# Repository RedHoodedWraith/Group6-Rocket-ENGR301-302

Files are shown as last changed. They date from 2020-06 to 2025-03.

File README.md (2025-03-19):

# Group 6's Rocket Project
## Introduction
This project was developed as part of an in-class group project to design and develop a hobbyist rocket that used on-board programmable electronics to control it and to collect and report on-board telemetry.</br>
It was developed in 2020 by students in Group 6 from the [ENGR301](https://www.wgtn.ac.nz/courses/engr/301/2020) & [ENGR302](https://www.wgtn.ac.nz/courses/engr/302/2020) courses at the Victoria University of Wellington in New Zealand. 

While the students who worked on this project passed the aforementioned courses, at the time of writing, this project is in an unfinished state and there is not functioning rocket.</br>
The courses, ENGR301 & ENGR302, were focused on developing our skills around working on technical projects as part of a development team that uses Agile Development Practices. In the context of the courses above, this project was worked on to put into practice what we had learnt and to demonstrate our skills relating to using Agile.

While this project is incomplete and isn't likely to be worked on, anyone is welcome to use what we have made so far and/or to finish it off.

## Contributors

### Software
* Asami De Almeida
* Ketaki Bagal
* Penny Peneuta

### Hardware
* Jason McCormick
* Sean Osborne-Curtis
* Robert Reid
* Dylan Sukha

### University Staff Involved
* Andre Geldenhuis
* Aaron Chen

## Modules:

### Software Development
* Sun Incinerator Rocket Controller | PID system
* Sensor Test Programs
    * MPLI2C | Barometer + temperature readings.
    * MPU | | Gyro + Acceleartion readings, IMU+Servo Control.

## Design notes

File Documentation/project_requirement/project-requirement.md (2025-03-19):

environmental# ENGR 301: Project Requirements Document

The aim of this document is to specify the requirements of the system your group is to build. The focus of a requirements document is the problem you are attempting to solve:  not a first attempt at a solution to that problem. This document should communicate clearly to the supervisor, client and course coordinator what the system you build is going to do, and what constraints it must meet while doing so.

The document should also demonstrate your understanding of the main analysis principles and quality guidelines, and applicable standards, using tools and notations as necessary to communicate the requirements precisely, unambiguously and clearly in a written technical document. Page specifications below are *limits not targets* and refer to the pages in the PDF generated from the markdown. Because the size of your document is necessarily limited, you should ensure that you focus your efforts on those requirements that are most important to completing a successful system: if sections are at their page limit, indicate how many items would be expected in a complete specification.

The ENGR 301 project proposal and requirements document should be based on the standard ISO/IEC/IEEE 29148:2011(E), primarily sections 8.4 and 9.5, plus section 9.4 for projects involving hardware and ISO 25010 SQuaRE for systemic requirements. While excerpts from the standard have been quoted within the template, to understand what is required it will be necessary to read earlier sections of the standards themselves. A supplementary treatment of requirements gathering in engineering projects may be found in [Requirements in Engineering Projects](https://victoria.rl.talis.com/items/F166DA94-DAD8-FBDB-0785-7A63C9BA3603.html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) (Talis). The requirements document should contain the sections listed below, and conform to the formatting rules listed at the end of this brief.

All team members are expected to contribute equally to the document and list their contributions in section 6 of the document. You should work on your document in your team's GitLab repository. While collective contributions are expected to be the exception rather than the rule, if more than one team member has contributed to a particular commit then all those team member IDs should be included in the first line of the git commit message. `git blame`, `git diff`, file histories, etc. will be tools used to assess individual contributions, so everyone is encouraged to contribute individually, commit early and commit often. Any team wishing to separate individually contributed sections into a single file before collation into the single proposal document for submission is welcome to do so.

---

# ENGR 301 Project *NN* Project Proposal and Requirements Document
#### Author list, a comma-separated list of the names of each member of the team.

## 1. Introduction

### Client

The Client for this project is Andre Geldhuis, and can be contacted by andre.geldenhuis@vuw.ac.nz or through Mattermost.

### 1.1 Purpose

The purpose of this system is to build off an existing rocket system and to improve its avionics and flight control.

### 1.2 Scope

The rocket being made for the client(s) listed above needs to be able to do the following:
*  Thrust itself from ground in order to launch itself into the air
*  Continue to propel itself in a largely vertical direction
*  Self-adjust propellant to its nozzle(s) in order to continue travelling in a controlled upwards direction
*  Travel upwards at a velocity that demonstrates the rocket is being controlled by its on-board control systems

The development of this rocket will happen in 3 core stages. Hardware design stage, software design stage and trial testing.
The Hardware Design Stage will focus on the physical build and design of the rocket, incorporating all the necessary components,
maximising travel efficiency and minimising the physical obstacles. The Software Design Stage will focus on programming the
on-board micro-controller to automatically adjust the rocket's propellants to self-correct the rocket's travel. Trial testing will
involve launching test rockets to observe how it performs in-situ and to return back to either design stages to modify the design to
 its performance. This project's development is limited by a variety of factors, most notably access to the internet and the civil restrictions in place due to the COVID-19 pandemic.
This heavily limits the availability to source parts for the rocket and opportunities to test the physical rocket prototype in-situ.

### 1.3 Product overview
#### 1.3.1 Product perspective

The project, in its entirety, is expected to address and solve the general issue of producing a controlled rocket using open-source software and open-hardware. The intended use for this rocket will primarily be for private operation but carries the potential for extended development and commercial use through being open-source.

The avionics element of the project must imitate the functionalities of a contemporary, off-the-shelf version and provide control features for the rocket as well. In particular, the system is required to manage various components of the rocket that ensure controlled flight such as, sensors, servos motors and transmitters.

In terms of the hardware component, the physical rocket model will be constructed from scratch, adapting the template of a basic hobby rocket that incorporates a gimballing motor for control. Additionally, an avionics board is to be assembled so that data can be remotely collected from the rocket and sensors. The software component will be developed to contribute in designing the control parameters for the avionics board.

The hardware and software components of the avionics package are required to seamlessly communicate with the mission control and simulation segments of the project to ensure a successful launch and flight for the rocket.

The avionics package will communicate with mission control to report its current pre-launch, launch and in-flight status. The simulation software will be used to aid in designing the rocket and determining estimates for the rocket control parameters. In this case, the software model of the control code developed in the avionics package will be required for simulation.

#### 1.3.2 Product functions

One page summary of the main functions of the product (9.5.4), briefly characterising the minimum viable product.

The minimum requirements for this avionics system will consist of the following:
- Record all sensor data which should collect data on a variety of benchmark measurements that include but are not limited to: stability, altitude, deviation, and critical components.
- Achieve an aerodynamically stable and consistent launch
- A demonstration of mission control's ability to adjust flight trajectory post-liftoff by instructing the gimble to turn, performing a kickover.
- After the motor has completed its burn, broadcast telemetry (location) over LoRa modules to a base station on the ground.
- An avionics package that is easy to install and uninstall.
- A hardware "On" and/or "Reset" switch that initialises launch in the event of a software launch failure.
- "Fast" hardware and software setup. Ideally, 10 minutes or less.
- Utilise onboard sensors and tuned error control to prolong vertical traversal. 
- Provide a compatible interface to be used in conjunction with a mission control system.
- Provide a compatible interface utilise simulation data for calibration ahead of time.

Ideally, the finalised package will incorporate the following:
- Support for parachute deployment.
- Provide control for aerodynamically stable launches without a rail.

#### 1.3.3 User characteristics   

The avionics package will be open-source meaning anyone can access it. However, the intended main class of users for this project is the wider model rocketry/high power rocketry community. And so general user characteristics which are expected include:

- An understanding of rocket avionics
- Technical expertise when installing different components of the rocket
- An understanding of those components and how they function within the system
- Technical expertise in telemetry systems
- An understanding of how the software will interact with the hardware
- Experience in operating aircraft applications
- Knowledge in Civil Aviation Authority (CAA) regulations

Due to health and safety concerns users testing the rocket in the field should not have any physical and or mental disabilities that would put them at risk.

#### 1.3.4 Limitations
Within project limitations, the team is faced with several limitations such as;
- Current worldwide affect(COVID-19): COVID-19 has resulted in a nationwide lockdown. This has limited the group options and approach towards the  current project. Certain aspects of the project will be adjusted from the original plan. The use of communication tools like Mattermost and  Zoom  will be crucial to the group.

- Budget: The team has a very limited budget of approximately $333.00 NZD. The budget has designed to be spent on components for the hardware as well as 3D printing for the rocket body.   

- Hardware accessibility: Due to the effect COVID-19 has had on the university, our hardware accessibility is been very limited. The extension of the hardware is improving on the control system of a previous team and on using *Onshape* to improve the design of the body of the rocket. 

- Software: The software aspect of the project is not very limited from the lockdown. The software aspect will consist of improving code from a previous team and ensuring it is functional and efficient.  

- Testing facilities: Due to COVID-19 lockdown, it will be unlikely that a testing facility is available for the group to use. The next step is to do testing via simulation. Working with a simulation team will be required. If circumstances change and access to testing facilities become available then the group will have to discuss the possible option.

- Time: This project runs over two papers ENGR 301 and ENGR 302. This gives the group 30 weeks, however with the first few weeks being introductions realistically the group has about ~27-26 weeks. The lockdown has resulted in a reconstruction of the academic year of Victoria            University of Wellington. This could result in less time.    

- Control & policies: When testing the rocket system we have designed, we need to ensure it is in a controlled environment. We can not breach any laws and restrictions that have been imposed by the government due to COVID-19 and we need follow The NZ Rocketry Association rules and regulations.  

- Team interactions: The main form of communication will be through Zoom and Mattermost due to the level 4 lockdown. Zoom meetings are held every Friday and Monday, and Mattermost chat is constant.

- Personal limitations: All members have personal limitations that should be taken into consideration. This will ensure all members of the group are treated fairly. Other members of the group as well, take other papers. Due dates of important assignments and test will be taken into account, this is design to reduce stress levels of the group.

## 2. References
[1] Civil Aviation Authority of New Zealand, “Civil Aviation Rules, Part 101 Gyrogliders and Parasails, Unmanned Aircraft (including Balloons), Kites, and Rockets Operating Rules” December 31st, 2018 [Online]. 
Available: https://www.aviation.govt.nz/assets/rules/consolidations/Part_101_Consolidation.pdf [Accessed: May 13th, 2020]. 

[2] National Aeronautics and Space Administration, Vectored Thrust, Glenn Research Center, Nancy Hall, 05 May 2015.
https://www.grc.nasa.gov/WWW/K-12/airplane/vecthrst.html

[3] New Zealand Legislation, Radiocommunications Regulations 2001, 10 September 2001. 
http://www.legislation.govt.nz/regulation/public/2001/0240/latest/DLM71513.html. 

[4] The Model Rocket, Model Rocket Engine Sizes and Classifications, Charlie Gasmire, 2020.
https://themodelrocket.com/model-rocket-engine-sizes-and-classifications/

[5] New Zealand Rocketry Association, “Rocket Safety, Model Rocketry Safety Code” [Online]. 
Available: https://www.nzrocketry.org.nz/rocketry/rocket-safety [Accessed: May 13th, 2020]

References to other documents or standards. Follow the IEEE Citation  Reference scheme, available from the [IEEE website](https://www.ieee.org/) (please use the search box). (1 page, longer if required)

## 3. Specific requirements  

This section describes the external interfaces, functions, usability requirements, performance requirements, logical database requirements, design constraints, non-functional system attributes, physical and environment requirements and supporting information.

### 3.1 External interfaces

#### Sensors - Inertial Measurement Unit

The inertial measurement unit (IMU) is an electronic device that measures acceleration, gyroscopic and magnetism data on the avionics package, each in 3 dimensions. This will be used to specifically measure the changes in the linear acceleration, velocity, and orientation of the rocket. The data from this unit will be outputted onto the SD card onboard where the Teensy will also process this information and control the position of the gimbal. This component of the system will require good accuracy plus tolerance as it is vital for the control of the rocket and will need to have a measurable acceleration range suitable for the rocket. The orientation and position of the rocket will be measured on 3 dimensions, in units of metres and degrees respectively. This will be present as part of the onboard avionics package.

#### Data Storage/Transfer - SD Card

An SD card is required to store data that is produced from the IMU, radio antenna, GPS and any other potential sensors. This information is to be processed for control and to be later used for the analysis of the performance of the system. The onboard system will need to be able to write to the SD card at a rate equivalent to the rocket's control loop. This rate will be required to be optimized so that it does not affect processing speed significantly while maintaining maximum control. The SD card must also be large enough to store all the potential data in a test run, with the data being stored in a .txt or .csv file.

#### Communication - Radio Antenna

The radio antenna is required for limited communication of data from the avionics package, using LoRa, to a nearby external computer for monitoring the data and minor adjustments/tuning. The antenna will receive signals from the avionics package and will output transmissions for a receiver antenna. The data sent will be required to be accurate enough to determine the state of the system in real-time and so it can be located easily using the satellite positioning system, GPS, in the case that it is lost. Data transferred during the launch will need to be essential data only as communication should not compromise performance of the control system.  The units of measure for this data will all be SI units and degrees/minutes/seconds for the longitude and latitude. This will play an important role for mission control in the field.

#### Mechanical - Gimbal

The rocket's gimbal will control the angle of the thrust relative to the centre of mass, thus stabilising and controlling the direction of the rocket's propulsion through the launch. This process is known as thrust vectoring. The gimbal will be controlled by the software on the avionics package which will adjust servos, altering the pitch and yaw. This will require a closed-loop control such as a Proportional-Integral-Derivative system, input from the IMU and outputting to the Gimbal.

#### Control Hardware - Servos

Two servo motors will be required to control the gimbal, that is controlled by an electric signal which determines the movement/angle of the shaft. This will be controlled from the avionics package and will alter the orientation of the gimbal. The servo's shaft rotation will be measured in degrees. The two motors will work individually, one to control the pitch and the other yaw. The timing response of this part is required to be minimised so that the rockets projection control can be as close to instantaneous as possible.

#### Ejection Ignition

The rocket will require a system to fire small igniters, which serve as ejection charges for the parachute. These are to be set off at a predetermined height for the descent of the rocket. This will receive its signal from the avionics package, which determines the height using the onboard barometer sensor. Some precaution is also required for the development of this component, as it will need to be ensured that it won't fire while the rocket is being handled.

#### Motor

The motor is a single-use component to produce the thrust for the rocket during the launch, by burning through a propellant which is released through a nozzle to produce powered flight. The ignition is required to be controlled by an electric igniter externally from the rocket for safety. This motor is to be connected to the gimbal, which will control the rocket. Motors vary in size depending on their total impulse, measured in Newton Seconds. This rocket will be required to use motors in the range of classes from C to G, ranging from 5-160 Ns. These motors likely to have a diameter of 24mm, and some of the smaller ones being 18mm.

### 3.2 Functions

> List up to fifty use cases (in order of priority for development),

#### Stakeholder Requirements:
- Avionics package must entirely fit inside the rocket's shell.
- Avionics package must interface with the gimbal.
- Avionics package must guide rocket on course.
- Avionics package must stabilise the rocket so it stands in an upright position while preparing for launch.
- Avionics package logical database will be comprehensible in the form of a text file.
- Avionics package should be comprised of fixated and durable components.
- Avionics package in the rocket must interface intuitively with the base station.
- Avionics package must ensure onboard power management can cope with each stage of the rocket's execution.

#### Use Cases:
Upon delivery to the primary client (Andre), the extended branch of stakeholders will include open-source hobbyists.
The purpose of this avionics package is to provide control and guidance for the rocket.
To do so, it needs to be installed, configured and calibrated prior to launch.
The user(s) should be able to expect recorded data from the flight.
The typical usage of the avionics package would look like:
Installation, calibration, launch, and post-flight analysis.

##### Installation
For ease of installation and reinstallation, the avionics package will uphold the following:
- Minimal physical footprint to mitigate spatial occupation and excess weight.
- Ensure as many components are fixated on a single unit rather than having components loose and untethered.
- Trouble-free pairing with the base station.

##### Configuration and Calibration
- The avionics package should be easy to configure for all intended stakeholders.
- The finished package should not require re-engineering to interface with control software during launch setup.
- Calibration data from simulations should be preloaded and initialised onto the avionics package prior to launch. Calibration is crucial as the standalone error control is likely not adequately fast enough to ensure stable control of the rocket.
- The calibration data will be stored on the SD card onboard the avionics package.
##### Launch
Once the rocket is launched into powered flight, the rocket will be remotely controlled via the gimbal to sustain vertical trajectory.
Vital flight data will be communicated with the base station in real time.
At the stage of burnout, the avionics package will be automated to deploy the parachute as a step to mitigate risk during the process of landing.
##### Analysis
The avionics package should broadcast vital data via its wireless antenna to the base station during flight. <br></br>
When the active flight is over, all logged data (measurements, instructions and gimbal positions) should be stored to the SD card, as a text file in a human-readable format.
If the avionics package is still in range of the wireless signal, it will attempt to broadcast the data to mission control. All data broadcasted to mission control must comply with the standards (units, parsing methods, encryption etc) of the mission control software.

### 3.3 Usability Requirements

The avionics package is usable if it is efficient and can successfully be operated and applied by no less than a rocket hobbyist. Therefore, the goal is to create an open-source avionics package that is accessible to the wider avionics community and applicable in all types of rocket-related use. The rocket should also be able to perform and endure through various external factors such as wind. This means that it is important to build a versatile avionics package that can withstand the external factors and mitigate the risks that follow.

In context, the avionics package will be used as a major component of a controlled rocket launch system. The effectiveness of the avionics package is measurable by its performance, which is contingent upon the success rate of a favourable launch and flight.

This is achieved by performing frequent in-flight correction of the gimbal position to ensure high efficiency and furthermore high performance. The software model of the avionics package will need to be designed in a way where it can easily be applied by the simulation segment of the larger system. As a result, this will contribute to improving the performance of the rocket gimbal.

Additionally, the software model should ideally be written using a common programming language used in avionics such as C to further improve its usability in the future. This will ensure that the software can be understood and applied by the regular avionics user.

In terms of the hardware component, it is essential that the avionics package is constructed in a way that is adaptable to changes that can occur at any point in time. The manual controls on the rocket should also be easily accessible to the user even after construction is completed.

**Uses**

Launch:

The rocket must be ready for launch within a set period of time following system activation.

In-flight:
- Diagnostics: The data from the rocket and sensors are remotely collected. This will diagnose any in-flight issues with the rocket.
- Recovery Mode: Once the motor burns out, recovery mode is enabled and the parachute is ejected.  

### 3.4 Performance requirements

This section defines the expectations of the rocket's functions and qualities, what the product should demonstrate to the user on a quantitative and qualitative level. The rocket will be constructed of many different functioning components, establishing a range of software and hardware performance requirements along with the rocket's general performance itself.

A key requirement of the rocket's performance is that it has a strong structural integrity, so that it is able to withstand stress, acceleration, velocity, vibration and heat that will be present during launch. This will ensure functionality and longevity of the rocket. It is required that the system can be tested at least 10 times, with any deficient parts after that to be easily replaced. The environment has a strong impact on the performance of the rocket, the most critical factor being the wind. Ideally the rocket will launch when there is minimal wind however this can be expected to increase with altitude. The system will be required to control the rocket in wind speeds up to 15 m/s. The general performance of the system is required to have a vertical-to-horizontal distance travelled ratio exceeding 90% at the completion of climbing flight.

The performance of the software will have a strong influence on the rocket's control so the system will require minimum delay between sensors and actuators. This delay will be determined by the maximum operating speeds of the components, such as the servos and the IMU. Another key aspect of the software performance is the communication of data through out each stage of the launch. It is essential that information to mission control is continuous. It is important to note that however this load will vary depending on the stage. The required data is the state of the rocket, the location and potentially some kinetic data. An additional software requirement is for a fast data rate on to the SD card, which will need to be taking readings from the sensors at least every 50ms more good analysis of the flight.

The core part of the systems performance is dependent on a power supply which makes the batteries performance vital. It is required that the system does not deplete more than 50% of the capacity throughout the launch process, leaving the remaining power for initiation and retrieval. This will be later detailed with more knowledge of the power consumption and specifications. It is also required that the servos are performing at a rotational speed sufficient enough to emulate the control system and also strong enough to manipulate gimbal. The geographical location of the rocket is important for finding it after launch so the GPS is required to perform within an error of 10 metres. To ensure communication during this stage the LoRa radio system will be required to transmit and receive up to 2 kilometres away, so the rocket may be retrieved if it was to travel far during descent. Like the structural integrity of the rocket, the individual components will need be able to with stand the induced environment factors during launch for longevity, this will require strong connections and a good quality of wiring. A vital part of the systems performance is that it is required to eject a parachute at the top of ascent, this needs to be certain so tests will be required to be implemented.

### 3.5 Logical database requirements

In order to analyse the system that will be implemented, the use of a domain model for the purpose of demonstrating the logical database requirements would be useful. For the purposes of this design, elements that will be implemented include the use of inertial motion unit (IMU) that are the sensors that collect the data that will be provided for the use of the overall system, including the controller. Additionally, this data will be fed into a microcontroller. Additional data that will be fed into the microcontroller is the GPS data. However, this data will not be used for the actual control of the system. Furthermore, data from the microcontroller will be sent to the SD Card Data Writer for the purpose of locally saving the flight data. And finally, there will be a radio module that will be used to broadcast the data to mission control remotely.

@startuml

title Relationships - Class Diagram

class IMU {
  +Gyrometer
  +Acceleromter
  +Magnetometer
}

class Microcontroller
class RadioModule
class GPSModule
class SDCardWriter

IMU --> Microcontroller
GPSModule --> Microcontroller
Microcontroller --> SDCardWriter
Microcontroller --> RadioModule

@enduml

**Gyroscope**

A gyroscope will collect data with reference to the potential rotation of the rocket with reference to the ground. This will be a key data point for the determination by the microcontroller on if or when any changes need to be made with respect to the gimble. Rotational energy that deviates outside of an expected range could lead to the rocket flying fully off course or even catastrophic failure.

**Accelerometer**

This device will measure the change in velocity and acceleration with reference to the acceleration of gravity. This data can be used to determine altitude which will be  a key point for the determination of apogee and the initialisation of any recovery hardware.

**Magnetometer**

A magnetometer in this device can be used for the purpose of designing a form of a digital compass that can determine which side of the rocket is facing a given cardinal direction with respect to the magnetic north pole. This data would be useful for the purpose of the microcontroller to determine if any gimbal adjustments need to be made if there is an imbalance in the rocket. Or, in other words, the mass of the rocket is not centred around a centre point of a cylindrical shape.

**GPS Module**

The device will be used to collect positional data at the cessation of the rocket launch to determine where the rocket's landing area is. This is particularly useful if there is an extreme deviation of the rocket landing area from the rocket launch area.

**Microcontroller**

The microcontroller will handle the general integration of all the IMU componenets. This collective data will be interpreted by the microcontroller to determine if any positional changes to the control gimble will need to be made. Accurate and calibrated data collection is essential for any practical use of the microcontroller for this system.

**SD Card Writer**

The SD card writer will be the component that keeps the log of all the data collected during the flight from the IMUs. Furthermore, it will log any changes made to gimble positions. Furthermore, these can be timestamped to correspond with specific values from the IMUs including any data that is calculated by the microcontroller for the purpose of determining flight changes. These could include altitude, reduction in acceleration, positional data, etc. 

**Radio Module**
The radio module will retain the purpose of being able to send radio data (including that which would be written to the SD card) to mission control. The collection of this data during flight would allow for mission control to determine if any manual changes need to be made that override the microcontroller. As such, this radio module would also need to be able to receive signals from mission control. 

You should use right tools, preferably PlantUML, to draw your URL diagrams which can be easily embedded into a Markdown file (PlantUML is also supported by GitLab and Foswiki).

### 3.6 Design constraints

**Software - Open Source**

For the final avionics package to qualify as open-source, only open-source resources may be used throughout its development. The open-source resources used must be well documented and credited, where needed, in the package release. Softwares, which are not open-source, may only be used if absolutely necessary and has been consented by the client. Once finished all source code for the package must be released in accordance with the open source definition.

**Software - API**

For consistency and compatibility across the three different sections, system engineering, mission control and rocket simulations, the same API should be used. Using the same API also ensures that the final avionics package will work as a whole.

**Hardware - Radio Antenna and the Satellite Navigation System Unit**

The radio antenna must follow the New Zealand Legislation, Regulation 9 of the Radiocommunications Regulations 2001 and only use the legally available frequencies with the rockets and solely for their intended purpose [3].

Similarly, the satellite navigation system unit used must also follow the New Zealand Legislation, Regulation 9 of the Radiocommunications Regulations 2001 and only use the legally available satellite navigation frequencies for New Zealand [3].

To avoid interference with nearby devices the radio antenna must use frequencies with the least use. Interference with other devices may result in corrupted data, which in turn could affect the satellite navigation system location of the rocket.

**Hardware - Physical Construction**

In accordance with the New Zealand Civil Aviation Authority and the New Zealand Rocketry Association, the rocket at its maximum size must satisfy the following criteria [1][5]:

- The rocket cannot use more than 125g of propellant
- The rocket cannot produce more than 320 Newton seconds of total impulse
- The rocket must use a slow-burning propellant
- The rocket is made from lightweight materials such as paper, wood, rubber and or plastic
- The rocket must not have the nose cone, fins or body fabricated from metal
- The rocket must not exceed a gross mass (i.e. including the propellant) of 1.5kg
- The rocket must not use an aerial firework as an ingredient to form its own jet
- The rocket must only use certified commercially-made model rocket motors
- The rocket motors must only be used in line with the manufacturer's recommendations (i.e. no tampering)
- The rocket must be launched with an electrical launch system and electrical motor igniters

The physical construction of the rocket will also be limited to our budget, what we have access to in the labs and (due to Covid-19) when. Similarly delays in shipments because of the virus will also limit us in what parts we can order online.

### 3.7 Nonfunctional system attributes

Present the systemic (aka nonfunctional) requirements of the product (see ISO/IEC 25010).
List up to twenty systemic requirements / attributes.
Write a short natural language description of the top nonfunctional requirements (approx. five pages).

1. Safety
   - The rocket's operations must not cause nor contribute to harm or death to people or animals, including but not limited to its operators, nearby bystanders, pets and the local biodiversity.
   - The rocket's operations must not cause damage to property nor the local environment external to its operational scope. Example: Burnt Fuel Residue to the launchpad is accepted as it is expected as part of its operation. Cracking the windscreen of a nearby vehicle is not acceptable.
   - Operators must be able to know sufficient real time information with regards to the condition, location and effects of the rocket during its operation.

1. Flight
   - The rocket needs to be able to thrust itself from the launchpad.
   - The rocket needs to be able to continue to propel itself upward when it is expected to do so.
   - The force exerted by the propellant needs to exceed the opposing forces, such as the force of gravity onto the rocket's mass and air resistance.

1. Robustness
   - The essential systems contributing to the rocket's flight must remain sufficiently intact during the rocket's operation.
   - Obstacles must not compromise the rocket's essential system processes that allows it to function.
   - The essential systems that contribute to the rocket's flight must be able to continue functioning when performing its task.
   - Essential system operations must not compromise each other system's functionality during their operations.

1. Control
   - The rocket's operation (during flight) must be sufficiently controlled by its operators.
   - Any unintended effects from the rocket's operation must be able to brought back into the control of the operators.
   - The rocket must be able to be controllable in order to increase Safety.
   - The rocket must be able to be brought back to a stationary or non-functioning state when expect it is expected to.
   - The rocket must be able to travel along the intended flight path of the operators' choosing.

1. Trackability
   - At minimum, sufficient data of the rocket's operation must be available to rocket's operators during its operation. This means data expected to be delivered in real time during the rocket's operation must be delivered in real time.
   - The rocket's location must be able to be monitored and known at all times during its operation, as per the requirement of Saftey and the Client's requirement.
   - Essential data that is not expected to be collected in real-time, must be able to be retrieved after the rocket's operation has ended.

1. Legal
   - This project must be performed legally and with the permission of the applicable property owner(s).
   - What we make and test must adhere to the rules and regulations of the relevant local authorities

### 3.8 Physical and Environmental Requirements
The system Hardware components:
- microcontroller(Teensy 3.6)
- gyroscope/accelerometer sensor
- sensor module(IMU)
- wireless antenna
- rocket motors
- servos
- gimble
- parachute + ejection charge
- rocket body
- launch pad (this includes, barometer, gps and the base station)

The hardware components must be able to still function within the environment that the rocket will be tested in, this means that the rocket will need to function under certain enviromental condition(s) that are present in the testing environment. The current testing environment is a wide-open park located in Upper Hutt, Wellington. A certain environmental condition is the wind. Wind levels are never constant and can vary extremely (especially in our testing environment of Upper Hutt Wellington). This means hardware of the rocket must be functioning under considerable wind levels. 

The largest effect wind has on the rocket is displacement. The wind is able to tilt (or even move) the rocket off its current trajectory. This means that hardware of the rocket must be to account for this issue. Combination of the electronic components (microcontroller, gyroscope and sensor module) and the gimble are involved in accounting for the displacement. Using the sensor(s) to detect the displacement, then micro-controller communicates to the gimble to make an adjustment for the displacement.

The rocket body design is also important to account for wind. A more aerodynamic design will mean that the wind drag will have less of the effect of the rocket. Meaning a more aerodynamic design will result in a smaller displacement.

Wind will also greatly affect the rocket while the rocket is coming down. The rocket slowly descend due to the parachute being deployed. However, with the parachute deployed the rocket is very susceptible to wind drag. Which means that the rocket might be displaced a large distance from the launch site. A GPS connected to the micro-controller will allow us to track where the rocket lands. Also, modelling of the rockets launch will be done to estimate where the rocket could land.

Another environmental condition that will need to be taken into account is radio frequency (RF) noise. To communicate to the rocket microcontroller we use a signal in the microwave frequency. So before we can launch the rocket, we will need to check the level of RF noise. If the level of RF noise is too high the launch of the rocket will be postpone, there is no solution where we launch the rocket in high RF noise. If the rocket is launch in during high RF noise we could lose communication with the rocket.

Certain envionmental conditions like rain, high cloud coverage and extreme temperatures will mean that the rocket launch won’t be able to happen. However, these conditions can be prevented by choosing a day launch where these conditions aren’t present. Finally the rocket should not be launch at night time.

### 3.9 Supporting information
The purpose project is to improve and partial redesign a previous module rocket, which includes an improved design of the avionics system, to ensure working and efficient code and possibly redesign the rocket hull to make it more aerodynamic. The end goal is to ensure a well develop rocket that is able to launch. Firstly we need to test the rocket via simulation, then working with mission control to physically test with a flight. 

By improving and developing this open-source rocket project we are able to present the rocket community with a possible new product. This resulting in new knowledge added to the model rocket community. This will hopefully lead to a better design module rocket.
## 4. Verification

3 pages outlining how you will verify that the product meets the most important specific requirements. The format of this section should parallel section 3 of your document (see 9.5.18). Wherever possible (especially systemic requirements) you should indicate testable acceptance criteria.

### 4.1 Verification External Interfaces
To verify the external interfaces of the system are meeting the specified requirements they will be tested in environmental conditions to simulate the launch, where their qualities can be formally verified. During these simulations it will be determined if the interfaces are fitting their purpose, working in the desired range, accuracy and/or tolerance, functioning with other interfaces, in the correct formats and meeting functioning specifications.

The IMU component will be verified by analysing the data and making sure it corresponds with the rocket's kinematics, this will also be reflected in the control system. The data transfer between the system and the SD card is verified after/or during a simulation or launch by reading the SD card and checks that it meets expectations. Wireless radio communication will be verified as the connection is tested over the potential distance range. The gimbal and servos performance requirements will be verified by meeting the specifications; moving in the full range of accurate angles, exerting enough force, and adequate response times. All these attributes will be measured. The ejection ignition interface will be verified by testing its response to input signals, and observing the outputs. Additionally doing a test run would be ideal. Since the motor is being outsourced, the only aspects of it to be verified is that it is the correct size and that the ignition operates.

### 4.2 Verification Functions

To meet the requirements of easy installation, the avionics package must be assembled into a single unit, with the exception of the battery unit. The avionics package must also be fixated with the rocket housing without any wobble.

To meet the requirements of intuitive configuration and calibration, the avionics package should be able to interface directly with the base station without having to re-engineer the hardware of software on either, the avionics package or mission control. Calibration data from the simulation teams must be transferred in a user-friendly manner, such as either directly writing to SD card or wirelessly via the base station. The software on the avionics package should not have to be manually recompiled from the toolchain.

To meet the requirements of the launch and flight phase, the rocket must launch and sustain vertical trajectory, even under mild weather interference. The avionics package must also allow mission control to remotely tilt the trajectory of the rocket in-flight. The rocket is also expected to land without taking on critical damage, though cosmetic wear is excusable. Throughout the launch and flight phase, power management must ensure a stable power supply system-wide meaning no components should malfunction due to inadequate power.

The analysis and diagnosis stage of the rocket's flight also has to meet requirements. Live data such as gyroscope and accelerometer readings must be broadcasted to mission control in real-time. By the end of the flight, the SD card must have all logged flight data recorded as a text file in a comprehensible format. The avionics package should also be able to broadcast all the logged data if still in wireless range. Mission control should be able to parse all broadcasted data.

### 4.3 Verification Usability Requirements

In order to meet the usability requirements, the avionics package must firstly achieve a successful launch and flight regardless of the external factors that may affect its performance. This can be measured by testing the rocket on different days in varied environmental conditions. If the rocket endures all tests with a satisfactory performance, the usability requirements have been passed. 

In terms of hardware, it is required that the avionics package be constructed in a way that is adaptable to change. This requirement is fulfilled when if at any stage of the development process modifications are required, the rocket will be able to adjust without complete deconstruction. 

Additionally, the software component should be open source and written applying a commonly-used programming language in avionics. The software model should also be programmed in a way that is understandable for other users. This can be shown by using effective code commenting and other types of documentation methods. In the context of this project, the software model of the source code should be accessible to the simulation developers and easily adaptable in order to aid in accurately estimating the PID control parameters. 

### 4.4 Verification Performance Requirements

The general performance of the rocket will be verified by inducing the environment conditions, software simulations of the launch and test flights. The structural integrity of the rocket will be verified by using simulation software and from there test flights. Also, visual inspection has the potential to show weaker parts. To verify the longevity of the rocket the system will need to have at least 10 test flights to be confident. The performance of the rocket's ascent will be verified by measuring the vertical climb and the GPS location to compute the vertical-to-horizontal distance travelled relationship.

The software's performance requirements will be more simple to verify as they should not require any physical flights. The delay between the sensors and actuators can be verified in the laboratory to get precise response times. Communication between the rocket and base station can be verified by simulating the rocket and using artificial data. The data rate and sample rates of the system can also be easily verified without test flights, using signal generators and comparing the data.

To verify the power consumption and supply performance requirements the systems will be tested multiple times over some time to see what the effect it has on the supply. This process can be broken down to determine the specific power consumption of each component. The performance of the servos will be verified in the laboratory by measuring their response to varying inputs similar to those expected in practice. The GPS performance can be verified by varying the location of the system and analysing the accuracy of the data according to how the system was moved. The radio communication can be tested by inducing the maximum transmission distance expected in similar terrain and reflecting on its performance. The structural integrity of the individual components will be verified during test flights and also a visual inspection. The final part of the hardware to be verified is the parachute ejection interface which can be tested without a flight to confirm functionality.

### 4.5 Verification Logical Database Requirements

As shown in section 3.5 of the UML class diagram, the relationship of how each abstracted component is interfaced is likely to hold consistent. 

From the perspective of the end user, the abstracted relationship of components plays no relevant role in the verification of the final product's performance. 

What will be required is that the documentation submitted has no conflicting design patterns and details with the finalised avionics package.

### 4.6 Verification Design Constraints

To meet the requirements of open-source for the software side of the avionics package, only open-source resources will be used throughout. Software that is not open-source may only be used with client consent.

To meet the requirements of a consistent API, the use and implementation of the same API will be discussed with the two other teams, mission control and rocket simulations. And then put into action accordingly.

To meet the requirements of the New Zealand regulations on the radio Antenna and the satellite navigation system unit the Radiocommunications Regulations 2001, Regulation 9 will be closely followed [3].

To meet the requirements of the New Zealand Civil Aviation Authority and the New Zealand Rocketry Association, on the rocket's physical construction, the design constraints laid out will be strictly followed [1][5]. 

To meet the requirements of our budget and deadline, rocket parts bought overseas will be limited to our budget and also to their shipment times.

### 4.7 Verification Nonfunctional System Attributes

1. Safety
   * Ensure there is adequate distance between people and the launch site.
   * Have a functioning fire extinguisher ready and on-hand during testing.
   * Choosing a wide-open space environment outdoors to perform the test it.
   * Cordon off the test area if need be.
   * Have someone watch where the rocket flies to and where it is falling.
   * Ensure that the rocket does not fly high enough it could hurt someone if it free fell.
   * Use of a parachute for freefall events.
   * Ensure there is a shutoff mechanism where applicable.

1. Flight
   * Testing the rocket with fuel.
   * Performing some calculations to figure out how much force should be exerted to lift the rocket and using sufficient amount rocket fuel.
   * Ensure the physical design is catered to follow the intended flight path.

1. Robustness
   * Testing each system before combining them.
   * Performing the tests on a small scale or in a simulated environment.
   * Deciding what the core systems are, checking if there are any process conflicts and amending the design to not conflict if there are conflicts (example of a conflict: a mechanism dislodges another mechanism).

1. Control
   * Have someone watch where the rocket flies to and where it is falling at all times during the test.
   * Ensure the physical design is catered to follow the intended flight path.
   * Ensure the rocket fuel is only loaded sufficient to its maximum intended use. Do not put in extra fuel if it's not planned to be used.
   * Ensure the correct amount of rocket fuel is ignited at the correct times.
   * Use of a parachute if a freefall is expected.
   * Ensure the rocket can communicate to mission control within a timely manner.

1. Trackability
   * Use of a GPS Receiver and a radio transmitter for data transmission for mission control to receive location data.
   * Have someone watch where the rocket flies to and where it is falling.
   * Have the rocket locally store desired and essential data, such as on an SD card, regardless of if it can be transmitted back to mission control.

1. Legal
   * Reviewing Civil Aviation Authority's rules and regulation for objects in flight.
   * Ensure the rocket does not fly high enough for other regulations to need to be applied.
   * Ensure the scope of the project keeps to the bounds of a hobbyist level activity.
   * Ensuring we have permission to use the land for testing from its property owner. If it is a park and the council permits the use of flying hobbyist level aircraft as part of their bylaw, this could be regarded as permission granted.

### 4.8 Verification Physical and Environmental Requirements
At this point of time, it is currently unclear of what hardware component can be sourced, and which need to be bought. The only known physical component that can be sourced is the 3D printed parts i.e the body of the rocket. These can be constructed and printed within the university. The hardware system which that makes up the avionics package (Teensy 3.6 microcontroller, gyroscope, IMU and the wireless antenna) will need to fit into the body of the rocket with the parachute and ejection charge. This needs to fit into a cone-like shape of 9X13 cm (9cm in height and 13cm in width).

The current testing location is a large park located in Upper Hutt, Wellington (the specific park is currently unknown). The day of launch will be planned ahead, meaning that weather conditions will be known in advanced. The optimum goal is to launch the rocket on a clear day (with very little to no wind). It possible for the weather to change or over environmental conditions to happen. Environmental conditions that prevent launch from happening are:
- rain/hail
- temperatures below 5 degrees celsius
- cloud coverage greater than 4 oktas
- high amounts of radiofrequency noise (enough to interfere with rocket communication)
- wind speeds greater than 30 km/h 

During rocket launch all requirements and regulations of both physical system and the Environment. The requirements and regulations must be able to be in line with the following organisations:
- NZ Rocketry Association
- Civil Aviation 
- Wellington region and local council  
- Victoria University of Wellington Faculty of Engineering and Computer Science 

## 5. Development schedule.

### 5.1 Schedule

#### Architectural prototype
The architectural prototype will be finalised by early April, and further developed. A more specific date is yet to be confirmed.
#### Minimum viable product
Due to Covid-19, the future of this project is very unclear, as a product may never physically be developed. However, being optimistic the minimum viable product would be available in late June. Also, to be confirmed in the near future with more information.
#### Further releases
The final prototype of the design will be completed by November 8th 2020 at the latest, being at the end of 2nd university trimester.

#### Delivery Method
Sections of work will be planned to be completed every 2 weeks in sprints. The content of these sections will be determined every fortnight on Monday and previous sprint will be reflected on.

### 5.2 Budget
Currently known components:

| Component | Purpose |  Price(NZD) |
|---|---|---|
| Teensy 3.6 board | Microcontroller for base station | $47.75 |
| Teensy 3.2 board | Microcontroller for rocket | $32.48 |
| 3D printing | Parts for rocket | depending |
| PCB | Cicuitry for rocket and/or base station | depending |
| Batteries | To power rocket | depending | 

Specific components to be confirmed: 

| Component | Previous team specific component | Price(NZD) |
|---|---|---|
| Radio transceiver |  RFM90 | ~$28 |
| GPS |  MPA‑154‑ANT L1 GPS | $9.45 |
| Servo | HK-282A | $8.21 |
| Servo | HC2422T 7.5kg | No longer continued |
| Signal receiver | FUNcube dongle | $33.83 |
| Voltage regulator | L7805 | $2.25 |
### 5.3 Risks

This table identifies the most important risks to achieving project goals. The majority of these risks comes down to product testing. The likelihood and impact for each of these risks have been rated on a value from 1-10. Based on how likely is it that it will occur and how much damage this would cause people, product, or development.

| **Risk** | **Risk Type** | **Likelihood** | **Impact** | **Mitigation Strategies** |
| --- | --- | --- | --- | --- |
| Premature motor ignition causing burns or injury  | Health & Safety | 4 | 5 | Hardware and software safety interlocks to reduce the chance of premature ignition. Keeping the motor away from heat sources or other potential igniters.|
| Premature Parachute Ignition causing burns or injury | Health & Safety  | 3 | 5 | Hardware and software safety interlocks will be required and also keeping the pyrotechnic charge away from heat sources or other potential igniters. |
| Flammable Surfaces during launch and landing | Environment Damage | 3 | 4 | The launch site will be required to have an absence of flammable material, such as dry grass. In addition, a fire extinguisher will be on hand ready for use. Also, emergency services may be called if needed. |
| High Winds/Excessive Drift causing damage to a person or property | Health & Safety/Environmental Damage | 5 | 4 | The forecast will be analysed prior to launch, and wind measurements exceeding the determined will result in cancelling the launch. Wind speeds at various altitudes will be taken into account. |
| Descending Rocket falling onto persons or property | Health & Safety/Environmental Damage | 4 | 6 | All participants will remain at least 10 meters from the launch site during launch and flight. All nearby public will be warned and the launch will only take place if the site is not busy, if the site does not exceed 10 people. The launch site will not be close to any private property or populated areas.|
| Descending debris falling onto persons or property | Health & Safety/Environmental Damage | 3 | 5 | The structural integrity of the rocket will be required to be very sturdy. All nearby public will be warned and the launch will only take place if the site is not busy, if the site does not exceed 10 people. The launch site will not be close to any private property or populated areas. |
| Intercepting other aircraft | Health & Safety | 2 | 7 | The maximum possible height will be determined and if this exceeds the minimum height for an aircraft, a NOTAM will be made to meet CAA regulations. In addition, the launch site will not be near any aerodrome to minimalise potential hazards. |
| Uncontrollable flight during launch | Health & Safety/Environmental Damage | 4 | 6 | All participants will remain at least 10 meters from the launch site during launch and flight. All nearby public will be warned and the launch will only take place if the site is not busy, if the site does not exceed 10 people. The launch site will not be close to any private property or populated areas. |
| Pandemic outbreak due to Covid-19 | Health & Safety/Development | 3 | 7 | Strategies to mitigate this problem vary with the state of Country. If an alert Level 2 or greater is in place, social distance will be implaced which will mean at home communication and development. |
| Crashing landing during test flights | Product Prototype | 2 | 5| To ensure the protoype is not damaged during test flights, vigorous tests will be implaced to make sure crucial elements are performing e.g parachute. |

### 5.4 Health and Safety

Document here project requirements for Health and Safety. All teams must state in this section:

1. How teams will manage computer-related risks such as Occupational Over Use, Cable management, etc.  

2. Whether project work requires work or testing at any external (off-campus) workplaces/sites. If so, state the team's plans for receiving a Health and Safety induction for the external workplaces/sites. If the team has already received such an induction, state the date it was received.

3. Whether project work requires the team test with human or animal subjects? If so, explain why there is no option but for the team to perform this testing, and state the team's plans for receiving Ethics Approval _prior_ to testing.

Also document in this section any additional discussions with the School Safety Officer regarding Health and Safety risks. Give any further information on relevant health and safety regulations, risks, and mitigations, etc.

#### 5.4.1 Safety Plans

Safety Plans may be required for some projects, depending on project requirements.
<br>
<br>Two questions all teams must answer are:

**Do project requirements involve anything that can cause serious harm or death?**  
Examples: building/modifying devices using voltages > 60 V, chemicals, large moving machinery, flying devices, bodies of water.

If so, you will have to write a separate Safety Plan as part of project requirements, and the Safety Plan must be referenced in this section. For health and safety risks involving serious harm or death, you must first contact the School Safety Officer and Course Coordinator first to discuss the Safety Plan and project requirements.

**Do project requirements involve anything that can cause harm or injury?**  
Examples: building/modifying things with voltages <= 60V, small moving machinery, wearable devices.

If so, you will have to write a separate Safety Plan as part of project requirements, and the Safety Plan must be referenced in this section. For health and safety risks involving harm or injury, you should write a draft of the Safety Plan before contacting the School Safety Officer and Course Coordinator to discuss the Safety Plan and project requirements.

If a safety plan is required, list in this section the date the School Safety officer accepted your Health and Safety plan (if accepted by submission date).

The project requirements may involve the risk of death, serious harm or injury to participants and members of the public. A safety plan is required to ensure all risks are addressed and planned for as the construction of the rocket progresses.  

## 6. Appendices
### 6.1 Assumptions and dependencies

### 6.2 Acronyms and abbreviations

CAA (Civil Aviation Authority): The Civil Aviation Authority of New Zealand is the government agency tasked with establishing civil aviation safety and security standards in New Zealand.

IMU (Inertial Measurement Unit): An inertial measurement unit is an electronic device that uses a combination of magnetometers, gyroscopes and accelerometers to measure the change of forces and movement.

NOTAM (Notice to Airmen): A notice to airmen is a notice filed with an aviation authority to alert aircraft pilots of potential hazards along a flight route or at a location that could affect the safety of the flight. 

IEEE (Institute of Electrical and Electronics Engineers): This is a professional association for electronic engineering and electrical engineering.

GPS (Global Positioning System): A GPS unit is actually a receiver that collects signals from satellites to determine location around the globe.

## 7. Contributions

| Name | Contribution/Section |
| ---- | ---- |
| Dylan Sukha | 3.2, 3.5, 4.2, 4.5 |
| Jason McCormick | 1.3.2, 3.5, 4.5|
| Ketaki Bagal | 1.3.3, 2, 3.6, 4.6, 5.4 |
| Penny Peneueta | 1.3.1, 3.3, 4.3, 5.4.1,  |
| Robert Reid | Project Charter, 2, 3.1, 3.4, 4.4, 4.1, 5.1, 5.3, 6.2, 7|
| Asami De Almeida |1.1, 1.2, 3.7, 4.7|
| Sean Osborne-Curtis |1.3.4, 3.8, 3.9, 4.8, 5.2|

---

## Formatting Rules

 * Write your document using [Markdown](https://gitlab.ecs.vuw.ac.nz/help/user/markdown#gitlab-flavored-markdown-gfm) and ensure you commit your work to your team's GitLab repository.
 * Major sections should be separated by a horizontal rule.

## Assessment  

The goal of a requirements document is the problem you are attempting to solve:  not a first attempt at a solution to that problem. The most important factor in the assessmernt of the document is how will it meet that goal. The document will be assessed for both presentation and content.

The presentation will be based on how easy it is to read, correct spelling, grammar, punctuation, clear diagrams, and so on.

The content will be assessed according to its clarity, consistency, relevance, critical engagement and a demonstrated understanding of the material in the course. We look for evidence these traits are represented and assess the level of performance against these traits. While being comprehensive and easy to understand, this document must be reasonably concise too. You will be affected negatively by writing a report with too many pages (far more than what has been suggested for each section above).

We aim to evaluate ENGR301 documents and projects as if they were real projects rather than academic exercises &mdash; especially as they are real projects with real clients. The best way to get a good mark in a document is to do the right thing for your project, your client, and your team. We encourage you to raise questions with your tutor or course staff, as soon as possible, so you can incorporate their feedback into your work.

---

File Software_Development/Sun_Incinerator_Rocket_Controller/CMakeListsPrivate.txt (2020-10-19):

# !!! WARNING !!! AUTO-GENERATED FILE, PLEASE DO NOT MODIFY IT AND USE
# https://docs.platformio.org/page/projectconf/section_env_build.html#build-flags
#
# If you need to override existing CMake configuration or add extra,
# please create `CMakeListsUser.txt` in the root of project.
# The `CMakeListsUser.txt` will not be overwritten by PlatformIO.

set(CMAKE_CONFIGURATION_TYPES "adafruit_feather_f405" CACHE STRING "Build Types reflect PlatformIO Environments" FORCE)

set(CLION_SVD_FILE_PATH "$ENV{HOME}/.platformio/platforms/ststm32/misc/svd/STM32F40x.svd" CACHE FILEPATH "Peripheral Registers Definitions File" FORCE)

SET(CMAKE_C_COMPILER "$ENV{HOME}/.platformio/packages/toolchain-gccarmnoneeabi/bin/arm-none-eabi-gcc")
SET(CMAKE_CXX_COMPILER "$ENV{HOME}/.platformio/packages/toolchain-gccarmnoneeabi/bin/arm-none-eabi-g++")
SET(CMAKE_CXX_FLAGS "-std=gnu++14 -fno-threadsafe-statics -fno-rtti -fno-exceptions -fno-use-cxa-atexit -mfpu=fpv4-sp-d16 -mfloat-abi=hard -Os -mcpu=cortex-m4 -mthumb -ffunction-sections -fdata-sections -Wall -nostdlib --param max-inline-insns-single=500")
SET(CMAKE_C_FLAGS "-std=gnu11 -mfpu=fpv4-sp-d16 -mfloat-abi=hard -Os -mcpu=cortex-m4 -mthumb -ffunction-sections -fdata-sections -Wall -nostdlib --param max-inline-insns-single=500")

SET(CMAKE_C_STANDARD 11)
set(CMAKE_CXX_STANDARD 14)

if (CMAKE_BUILD_TYPE MATCHES "adafruit_feather_f405")
    add_definitions(-D'PLATFORMIO=40304')
    add_definitions(-D'STM32F405xx')
    add_definitions(-D'STM32F4xx')
    add_definitions(-D'ARDUINO=10808')
    add_definitions(-D'ARDUINO_ARCH_STM32')
    add_definitions(-D'ARDUINO_ADAFRUIT_FEATHER_F405')
    add_definitions(-D'BOARD_NAME=\"ADAFRUIT_FEATHER_F405\"')
    add_definitions(-D'HAL_UART_MODULE_ENABLED')

    include_directories("${CMAKE_CURRENT_LIST_DIR}/include")
    include_directories("${CMAKE_CURRENT_LIST_DIR}/src")
    include_directories("${CMAKE_CURRENT_LIST_DIR}/lib/Lars_Main")
    include_directories("${CMAKE_CURRENT_LIST_DIR}/lib/Rutile_Servo_Controller")
    include_directories("${CMAKE_CURRENT_LIST_DIR}/lib/Rhodonite_External_Sensors")
    include_directories("${CMAKE_CURRENT_LIST_DIR}/lib/Padparadscha_Communications")
    include_directories("${CMAKE_CURRENT_LIST_DIR}/lib/Fluoride_Maintenence")
    include_directories("$ENV{HOME}/.platformio/packages/framework-arduinoststm32/cores/arduino/avr")
    include_directories("$ENV{HOME}/.platformio/packages/framework-arduinoststm32/cores/arduino/stm32")
    include_directories("$ENV{HOME}/.platformio/packages/framework-arduinoststm32/cores/arduino/stm32/LL")
    include_directories("$ENV{HOME}/.platformio/packages/framework-arduinoststm32/cores/arduino/stm32/usb")
    include_directories("$ENV{HOME}/.platformio/packages/framework-arduinoststm32/cores/arduino/stm32/OpenAMP")
    include_directories("$ENV{HOME}/.platformio/packages/framework-arduinoststm32/cores/arduino/stm32/usb/hid")
    include_directories("$ENV{HOME}/.platformio/packages/framework-arduinoststm32/cores/arduino/stm32/usb/cdc")
    include_directories("$ENV{HOME}/.platformio/packages/framework-arduinoststm32/system/Drivers/STM32F4xx_HAL_Driver/Inc")
    include_directories("$ENV{HOME}/.platformio/packages/framework-arduinoststm32/system/Drivers/STM32F4xx_HAL_Driver/Src")
    include_directories("$ENV{HOME}/.platformio/packages/framework-arduinoststm32/system/STM32F4xx")
    include_directories("$ENV{HOME}/.platformio/packages/framework-arduinoststm32/system/Middlewares/ST/STM32_USB_Device_Library/Core/Inc")
    include_directories("$ENV{HOME}/.platformio/packages/framework-arduinoststm32/system/Middlewares/ST/STM32_USB_Device_Library/Core/Src")
    include_directories("$ENV{HOME}/.platformio/packages/framework-arduinoststm32/system/Middlewares/OpenAMP")
    include_directories("$ENV{HOME}/.platformio/packages/framework-arduinoststm32/system/Middlewares/OpenAMP/open-amp/lib/include")
    include_directories("$ENV{HOME}/.platformio/packages/framework-arduinoststm32/system/Middlewares/OpenAMP/libmetal/lib/include")
    include_directories("$ENV{HOME}/.platformio/packages/framework-arduinoststm32/system/Middlewares/OpenAMP/virtual_driver")
    include_directories("$ENV{HOME}/.platformio/packages/framework-cmsis/CMSIS/Core/Include")
    include_directories("$ENV{HOME}/.platformio/packages/framework-arduinoststm32/system/Drivers/CMSIS/Device/ST/STM32F4xx/Include")
    include_directories("$ENV{HOME}/.platformio/packages/framework-arduinoststm32/system/Drivers/CMSIS/Device/ST/STM32F4xx/Source/Templates/gcc")
    include_directories("$ENV{HOME}/.platformio/packages/framework-cmsis/CMSIS/DSP/Include")
    include_directories("$ENV{HOME}/.platformio/packages/framework-arduinoststm32/cores/arduino")
    include_directories("$ENV{HOME}/.platformio/packages/framework-arduinoststm32/variants/FEATHER_F405")
    include_directories("$ENV{HOME}/.platformio/lib/Adafruit Unified Sensor")
    include_directories("$ENV{HOME}/.platformio/lib/Arduino_JSON_ID6249/src")
    include_directories("$ENV{HOME}/.platformio/lib/Blynk/src")
    include_directories("$ENV{HOME}/.platformio/lib/Bridge_ID945/src")
    include_directories("$ENV{HOME}/.platformio/lib/DHT sensor library")
    include_directories("$ENV{HOME}/.platformio/packages/framework-arduinoststm32/libraries/CMSIS_DSP/src")
    include_directories("$ENV{HOME}/.platformio/packages/framework-arduinoststm32/libraries/EEPROM/src")
    include_directories("$ENV{HOME}/.platformio/packages/framework-arduinoststm32/libraries/IWatchdog/src")
    include_directories("$ENV{HOME}/.platformio/packages/framework-arduinoststm32/libraries/Keyboard/src")
    include_directories("$ENV{HOME}/.platformio/packages/framework-arduinoststm32/libraries/Mouse/src")
    include_directories("$ENV{HOME}/.platformio/packages/framework-arduinoststm32/libraries/SPI/src")
    include_directories("$ENV{HOME}/.platformio/packages/framework-arduinoststm32/libraries/Servo/src")
    include_directories("$ENV{HOME}/.platformio/packages/framework-arduinoststm32/libraries/SoftwareSerial/src")
    include_directories("$ENV{HOME}/.platformio/packages/framework-arduinoststm32/libraries/SrcWrapper/src")
    include_directories("$ENV{HOME}/.platformio/packages/framework-arduinoststm32/libraries/Wire/src")
    include_directories("$ENV{HOME}/.platformio/packages/toolchain-gccarmnoneeabi/arm-none-eabi/include/c++/9.2.1")
    include_directories("$ENV{HOME}/.platformio/packages/toolchain-gccarmnoneeabi/arm-none-eabi/include/c++/9.2.1/arm-none-eabi")
    include_directories("$ENV{HOME}/.platformio/packages/toolchain-gccarmnoneeabi/lib/gcc/arm-none-eabi/9.2.1/include-fixed")
    include_directories("$ENV{HOME}/.platformio/packages/toolchain-gccarmnoneeabi/lib/gcc/arm-none-eabi/9.2.1/include")
    include_directories("$ENV{HOME}/.platformio/packages/toolchain-gccarmnoneeabi/arm-none-eabi/include")
    include_directories("$ENV{HOME}/.platformio/packages/tool-unity")

    FILE(GLOB_RECURSE EXTRA_LIB_SOURCES
        ${CMAKE_CURRENT_LIST_DIR}/.pio/libdeps/adafruit_feather_f405/*.*
    )
endif()

FILE(GLOB_RECURSE SRC_LIST
    ${CMAKE_CURRENT_LIST_DIR}/src/*.*
    ${CMAKE_CURRENT_LIST_DIR}/lib/*.*
)

list(APPEND SRC_LIST ${EXTRA_LIB_SOURCES})

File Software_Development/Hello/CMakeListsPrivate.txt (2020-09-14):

# !!! WARNING !!! AUTO-GENERATED FILE, PLEASE DO NOT MODIFY IT AND USE
# https://docs.platformio.org/page/projectconf/section_env_build.html#build-flags
#
# If you need to override existing CMake configuration or add extra,
# please create `CMakeListsUser.txt` in the root of project.
# The `CMakeListsUser.txt` will not be overwritten by PlatformIO.

set(CMAKE_CONFIGURATION_TYPES "adafruit_feather_f405;uno;" CACHE STRING "Build Types reflect PlatformIO Environments" FORCE)

set(CLION_SVD_FILE_PATH "$ENV{HOME}/.platformio/platforms/ststm32/misc/svd/STM32F40x.svd" CACHE FILEPATH "Peripheral Registers Definitions File" FORCE)

SET(CMAKE_C_COMPILER "$ENV{HOME}/.platformio/packages/toolchain-gccarmnoneeabi/bin/arm-none-eabi-gcc")
SET(CMAKE_CXX_COMPILER "$ENV{HOME}/.platformio/packages/toolchain-gccarmnoneeabi/bin/arm-none-eabi-g++")
SET(CMAKE_CXX_FLAGS "-std=gnu++14 -fno-threadsafe-statics -fno-rtti -fno-exceptions -fno-use-cxa-atexit -mfpu=fpv4-sp-d16 -mfloat-abi=hard -Os -mcpu=cortex-m4 -mthumb -ffunction-sections -fdata-sections -Wall -nostdlib --param max-inline-insns-single=500")
SET(CMAKE_C_FLAGS "-std=gnu11 -mfpu=fpv4-sp-d16 -mfloat-abi=hard -Os -mcpu=cortex-m4 -mthumb -ffunction-sections -fdata-sections -Wall -nostdlib --param max-inline-insns-single=500")

SET(CMAKE_C_STANDARD 11)
set(CMAKE_CXX_STANDARD 14)

if (CMAKE_BUILD_TYPE MATCHES "adafruit_feather_f405")
    add_definitions(-D'PLATFORMIO=40304')
    add_definitions(-D'STM32F405xx')
    add_definitions(-D'STM32F4xx')
    add_definitions(-D'ARDUINO=10808')
    add_definitions(-D'ARDUINO_ARCH_STM32')
    add_definitions(-D'ARDUINO_ADAFRUIT_FEATHER_F405')
    add_definitions(-D'BOARD_NAME=\"ADAFRUIT_FEATHER_F405\"')
    add_definitions(-D'HAL_UART_MODULE_ENABLED')

    include_directories("${CMAKE_CURRENT_LIST_DIR}/include")
    include_directories("${CMAKE_CURRENT_LIST_DIR}/src")
    include_directories("$ENV{HOME}/.platformio/packages/framework-arduinoststm32/cores/arduino/avr")
    include_directories("$ENV{HOME}/.platformio/packages/framework-arduinoststm32/cores/arduino/stm32")
    include_directories("$ENV{HOME}/.platformio/packages/framework-arduinoststm32/cores/arduino/stm32/LL")
    include_directories("$ENV{HOME}/.platformio/packages/framework-arduinoststm32/cores/arduino/stm32/usb")
    include_directories("$ENV{HOME}/.platformio/packages/framework-arduinoststm32/cores/arduino/stm32/OpenAMP")
    include_directories("$ENV{HOME}/.platformio/packages/framework-arduinoststm32/cores/arduino/stm32/usb/hid")
    include_directories("$ENV{HOME}/.platformio/packages/framework-arduinoststm32/cores/arduino/stm32/usb/cdc")
    include_directories("$ENV{HOME}/.platformio/packages/framework-arduinoststm32/system/Drivers/STM32F4xx_HAL_Driver/Inc")
    include_directories("$ENV{HOME}/.platformio/packages/framework-arduinoststm32/system/Drivers/STM32F4xx_HAL_Driver/Src")
    include_directories("$ENV{HOME}/.platformio/packages/framework-arduinoststm32/system/STM32F4xx")
    include_directories("$ENV{HOME}/.platformio/packages/framework-arduinoststm32/system/Middlewares/ST/STM32_USB_Device_Library/Core/Inc")
    include_directories("$ENV{HOME}/.platformio/packages/framework-arduinoststm32/system/Middlewares/ST/STM32_USB_Device_Library/Core/Src")
    include_directories("$ENV{HOME}/.platformio/packages/framework-arduinoststm32/system/Middlewares/OpenAMP")
    include_directories("$ENV{HOME}/.platformio/packages/framework-arduinoststm32/system/Middlewares/OpenAMP/open-amp/lib/include")
    include_directories("$ENV{HOME}/.platformio/packages/framework-arduinoststm32/system/Middlewares/OpenAMP/libmetal/lib/include")
    include_directories("$ENV{HOME}/.platformio/packages/framework-arduinoststm32/system/Middlewares/OpenAMP/virtual_driver")
    include_directories("$ENV{HOME}/.platformio/packages/framework-cmsis/CMSIS/Core/Include")
    include_directories("$ENV{HOME}/.platformio/packages/framework-arduinoststm32/system/Drivers/CMSIS/Device/ST/STM32F4xx/Include")
    include_directories("$ENV{HOME}/.platformio/packages/framework-arduinoststm32/system/Drivers/CMSIS/Device/ST/STM32F4xx/Source/Templates/gcc")
    include_directories("$ENV{HOME}/.platformio/packages/framework-cmsis/CMSIS/DSP/Include")
    include_directories("$ENV{HOME}/.platformio/packages/framework-arduinoststm32/cores/arduino")
    include_directories("$ENV{HOME}/.platformio/packages/framework-arduinoststm32/variants/FEATHER_F405")
    include_directories("$ENV{HOME}/.platformio/lib/Adafruit Unified Sensor")
    include_directories("$ENV{HOME}/.platformio/lib/Arduino_JSON_ID6249/src")
    include_directories("$ENV{HOME}/.platformio/lib/Blynk/src")
    include_directories("$ENV{HOME}/.platformio/lib/Bridge_ID945/src")
    include_directories("$ENV{HOME}/.platformio/lib/DHT sensor library")
    include_directories("$ENV{HOME}/.platformio/packages/framework-arduinoststm32/libraries/CMSIS_DSP/src")
    include_directories("$ENV{HOME}/.platformio/packages/framework-arduinoststm32/libraries/EEPROM/src")
    include_directories("$ENV{HOME}/.platformio/packages/framework-arduinoststm32/libraries/IWatchdog/src")
    include_directories("$ENV{HOME}/.platformio/packages/framework-arduinoststm32/libraries/Keyboard/src")
    include_directories("$ENV{HOME}/.platformio/packages/framework-arduinoststm32/libraries/Mouse/src")
    include_directories("$ENV{HOME}/.platformio/packages/framework-arduinoststm32/libraries/SPI/src")
    include_directories("$ENV{HOME}/.platformio/packages/framework-arduinoststm32/libraries/Servo/src")
    include_directories("$ENV{HOME}/.platformio/packages/framework-arduinoststm32/libraries/SoftwareSerial/src")
    include_directories("$ENV{HOME}/.platformio/packages/framework-arduinoststm32/libraries/SrcWrapper/src")
    include_directories("$ENV{HOME}/.platformio/packages/framework-arduinoststm32/libraries/Wire/src")
    include_directories("$ENV{HOME}/.platformio/packages/toolchain-gccarmnoneeabi/arm-none-eabi/include/c++/9.2.1")
    include_directories("$ENV{HOME}/.platformio/packages/toolchain-gccarmnoneeabi/arm-none-eabi/include/c++/9.2.1/arm-none-eabi")
    include_directories("$ENV{HOME}/.platformio/packages/toolchain-gccarmnoneeabi/lib/gcc/arm-none-eabi/9.2.1/include-fixed")
    include_directories("$ENV{HOME}/.platformio/packages/toolchain-gccarmnoneeabi/lib/gcc/arm-none-eabi/9.2.1/include")
    include_directories("$ENV{HOME}/.platformio/packages/toolchain-gccarmnoneeabi/arm-none-eabi/include")
    include_directories("$ENV{HOME}/.platformio/packages/tool-unity")

    FILE(GLOB_RECURSE EXTRA_LIB_SOURCES
        ${CMAKE_CURRENT_LIST_DIR}/.pio/libdeps/adafruit_feather_f405/*.*
    )
endif()

if (CMAKE_BUILD_TYPE MATCHES "uno")
    add_definitions(-D'PLATFORMIO=40304')
    add_definitions(-D'ARDUINO_AVR_UNO')
    add_definitions(-D'F_CPU=16000000L')
    add_definitions(-D'ARDUINO_ARCH_AVR')
    add_definitions(-D'ARDUINO=10808')
    add_definitions(-D'__AVR_ATmega328P__')

    include_directories("${CMAKE_CURRENT_LIST_DIR}/include")
    include_directories("${CMAKE_CURRENT_LIST_DIR}/src")
    include_directories("$ENV{HOME}/.platformio/packages/framework-arduino-avr/cores/arduino")
    include_directories("$ENV{HOME}/.platformio/packages/framework-arduino-avr/variants/standard")
    include_directories("$ENV{HOME}/.platformio/lib/Adafruit Unified Sensor")
    include_directories("$ENV{HOME}/.platformio/lib/Arduino_JSON_ID6249/src")
    include_directories("$ENV{HOME}/.platformio/lib/Blynk/src")
    include_directories("$ENV{HOME}/.platformio/lib/Bridge_ID945/src")
    include_directories("$ENV{HOME}/.platformio/lib/DHT sensor library")
    include_directories("$ENV{HOME}/.platformio/packages/framework-arduino-avr/libraries/EEPROM/src")
    include_directories("$ENV{HOME}/.platformio/packages/framework-arduino-avr/libraries/HID/src")
    include_directories("$ENV{HOME}/.platformio/packages/framework-arduino-avr/libraries/SPI/src")
    include_directories("$ENV{HOME}/.platformio/packages/framework-arduino-avr/libraries/SoftwareSerial/src")
    include_directories("$ENV{HOME}/.platformio/packages/framework-arduino-avr/libraries/Wire/src")
    include_directories("$ENV{HOME}/.platformio/packages/toolchain-atmelavr/lib/gcc/avr/5.4.0/include-fixed")
    include_directories("$ENV{HOME}/.platformio/packages/toolchain-atmelavr/lib/gcc/avr/5.4.0/include")
    include_directories("$ENV{HOME}/.platformio/packages/toolchain-atmelavr/avr/include")
    include_directories("$ENV{HOME}/.platformio/packages/tool-unity")

    FILE(GLOB_RECURSE EXTRA_LIB_SOURCES
        ${CMAKE_CURRENT_LIST_DIR}/.pio/libdeps/uno/*.*
    )
endif()

FILE(GLOB_RECURSE SRC_LIST
    ${CMAKE_CURRENT_LIST_DIR}/src/*.*
    ${CMAKE_CURRENT_LIST_DIR}/lib/*.*
)

list(APPEND SRC_LIST ${EXTRA_LIB_SOURCES})

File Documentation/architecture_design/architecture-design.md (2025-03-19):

# ENGR 301 Group 6 Architectural Design and Proof-of-Concept

Dylan Sukha, Jason McCormick, Ketaki Bagal, Penny Peneueta, Robert Reid, Asami De Almeida, Sean Osborne-Curtis

## 1. Introduction

The development of rockets over the last few decades has driven technlogy to grow in many different aspects that affect our everyday lives. Model rockets has become a growing concept globally that has expanded the knowledge and interest greatly. Rockets are susceptible to a variety of disturbances during flight, particular duirng the early stages. Such as unexpected winds, irregulatory and non-symmetrical motors, imparting a random launch angle. These result in unstable flight, by implementing an active control system we can cope with these undesired attributes.

The project aims to investigate and develop an existing avionics control and rocket system. This will implement the further design of an active control which will provide changes depending on the measured state of the rocket using sensors and actuators. This development will be supported by other teams working on a mission control aspect and others focusing on simulation of the rocket and flight.

### Client

Andre Geldenhuis is the client for this project. He can be contacted through email, Andre.Geldenhuis@vuw.ac.nz, or through the mattermost. He is an experienced rocket enthusiast and is a member of the New Zealand Rocketry Association who was the previous client of the 2018 project. His previous experience within the model rocket community is with launching model rockets from high altitude balloons. 

### 1.1 Purpose

The purpose of this system is to develop an existing rocket system and to improve its avionics and flight control, while also developing project managment skills.

### 1.2 Scope

For this project, we are improving and/or fixing a previous team initial system design of a model rocket. Due to the current worldwide event (COVID-19), we have not been able to access hardware. This means that it still a little unclear what exactly requires fixing and what requires improvement. The current task that will need to be down are the following: 
Take the existing avionics board and make it functional work 
To produce a base station to communicate with the rocket 
To develop and/or fix code to get the rocket functioning 
To redesign any parts (I.E body or gimbal) if the said part is not functioning or efficient 

### 1.3 Changes to requirements

If the requirement have changed significantly since the requirements document, outline the changes here. Changes must be justified and supported by evidences, i.e., they must be substantiated. (max one page, only if required)

## 2. References

References to other documents or standards. Follow the IEEE Citation Reference scheme, available from the [IEEE website](https://ieee-dataport.org/sites/default/files/analysis/27/IEEE%20Citation%20Guidelines.pdf) (PDF; 20 KB). (1 page, longer if required)

## 3. Architecture

Describe your system's architecture according to ISO/IEC/IEEE 42010:2011(E), ISO/IEC/IEEE 12207, ISO/IEC/IEEE 15289 and ISO/IEC/IEEE 15288.

Note in particular the note to clause 5 of 42010:

_"The verb include when used in Clause 5 indicates that either the information is present in the architecture description or reference to that information is provided therein."_

This means that you should refer to information (e.g. risks, requirements, models) in this or other documents rather than repeat information.

### 3.1 Stakeholders

See ISO/IEC/IEEE 42010 clause 5.3 and ISO/IEC/IEEE 12207 clause 6.4.4.3(2).

For most systems this will be about 2 pages, including a table mapping concerns to stakeholder.

#### Client 
The client for the rocket project is Andre Geldenhuis. 
For the project, the client requires the avionics package to strictly comply with certain specifications both, software-related and hardware-related. 

#### School of Engineering and Computer Science (ECS)

#### Software Developers and Testers

#### Wider Rocketry Community
The wider rocketry community consists of persons with a profound interest in rocket-related development and innovation. The expectation is that information regarding the avionics package and rocket will be available and usable by the community. 

#### Civil Aviation Authority (CAA)
The Civil Aviation Authorities of New Zealand establish and maintain the rules that all pilots, engineers, aircraft operators, airlines and aerodromes must follow to keep flying safe. The avionics package must follow suit.

#### New Zealand Student Space Association (NZSSA)
The New Zealand Student Space Association (NZSSA) is a student-run organisation with the intentions of following the progress made on the avionics package and rocket. 

#### Local Council
The local council includes the following authoritative bodies: Wellington City Council, Hutt City Council and Upper Hutt City Council. As a collective, the three councils ensure that laws and regulations are complied with in their respective region. In relation to the avionics package, the local council will guarantee that the build and launch of the rocket is compliant with model rocket use requirements in the area. 

#### Local Residents
The local residents include persons who reside in the greater Wellington Region, specifically Upper Hutt City residents that populate the surrounding area of the launch site. 

| Stakeholder  | Concerns |
|---|---|
| Client | The avionics package must be comprised of fixated and durable components, and should not exceed the specified size of the rocket airframe. It is also expected that the avionics package will interface with the base station and the gimbal to guide the rocket in-flight. Additionally, the avionics package should stabilise the rocket in an upright position pre-launch. The onboard power management must also be able to cope with each state of the rocket's execution. The avionics package-related information and data must be open source and published on the client's GitHub. The concerns listed are acknowledged in order to ensure a successful product for the client. |
|  Civil Aviation Authority (CAA) | The CAA requires that all rockets conform to all regulations set out in the CAA rules Part 101 Gyrogliders and Parasails, Unmanned Aircraft (including Balloons), Kites, and Rockets Operating Rules [1]. |
| School of Engineering and Computer Science (ECS) | The VUW School of engineering and Computer Science requires all parts of the project; to be correctly licensed and follow all relevant guidelines set out by ECS (including but not limited to open software, health and safety, copyrighting, plagiarism etc). |
| Software Developers and Testers | The Software Developers / Testers require that the avionics package complies with relevant open software and ethics rules.
| Wider Rocketry Community |  The rocket project must be open source and available to the wider rocketry community. Open source software operates under a license that provides users with the rights to freely use, modify and distribute the software. In this case, the rocketry community would benefit greatly from the rocket project if it is open source, as it can be adapted to future developments. |
|  New Zealand Student Space Association (NZSSA) |  The New Zealand Student Space Association (NZSSA) should regularly be kept up-to-date on the development of the avionics package and rocket. The organisation will be able to provide useful advice and information if they are often updated on the progress of the rocket. |
| Local Council  | The local council requires that the rocket does not violate model rocket use-related laws and regulations. In addition, the council will strictly require that the launch and flight of the rocket does not pose a risk to persons in the vicinity or damage to property in the surrounding area. |
| Local Residents | The local residents require an ensurity to their safety. And so the avionics package must conform to all relevant safety regulations and guidelines from relevant organisations and ruling bodies.  |

### 3.2 Architectural Viewpoints
(1 page, 42010 5.4) 

Identify the architectural viewpoints you will use to present your system's architecture. Write one sentence to outline each viewpoint. Show which viewpoint frames which architectural concern.

### 4. Architectural Views

(5 sub-sections of 2 pages each sub-section, per 42010, 5.5, 5.6, with reference to Annex F of both 12207 and 15288) 

Describe your system's architecture in a series of architectural views, each view corresponding to one viewpoint.

You should include views from the following viewpoints (from Kruchten's 4+1 model):

 * Logical
 * Development
 * Process
 * Physical 
 * Scenarios - present scenarios illustrating how two of your most important use cases are supported by your architecture

As appropriate you should include the following viewpoints:

 * Circuit Architecture
 * Hardware Architecture

Each architectural view should include at least one architectural model. If architectural models are shared across views, refer back to the first occurrence of that model in your document, rather than including a separate section for the architectural models.

### 4.1 Logical
...

### 4.2 Development
...

### 4.3 Process
...

### 4.4 Physical 
...

### 4.5 Scenarios
...

## 5. Development Schedule

_For each subsection, make clear what (if anything) has changed from the requirements document._ If unchanged, these sections should be copied over from the requirements document, not simply cross-referenced.

Schedules must be justified and supported by evidences; they must be either direct client requirements or direct consequences of client requirements. If the requirements document did not contain justifications or supporting evidences, then both must be provided here.

### 5.1 Schedule

Identify dates for key project deliverables:

1. prototype(s).
1. first deployment to the client.
1. further improvements required or specified by the client.

(1 page).

### 5.2 Budget and Procurement

#### 5.2.1 Budget

Present a budget for the project (as a table), showing the amount of expenditure the project requires and the date(s) on which it will be incurred. Substantiate each budget item by reference to fulfilment of project goals (one paragraph per item).

(1 page). 

#### 5.2.2 Procurement

Present a table of goods or services that will be required to deliver project goals and specify how they are to be procured (e.g. from the School or from an external organisation). These may be software applications, libraries, training or other infrastructure, including open source software. Justify and substantiate procurement with reference to fulfilment of project goals, one paragraph per item.
(1 page).

### 5.3 Risks 

Identify the ten most important project risks: their type, likelihood, impact, and mitigation strategies (3 pages).

### 5.4 Health and Safety

Document here project requirements for Health and Safety.

#### 5.4.1 Safety Plans

Safety Plans may be required for some projects, depending on project requirements.

## 6. Appendices

### 6.1 Assumptions and dependencies 

One page on assumptions and dependencies (9.5.7) 

### 6.2 Acronyms and abbreviations

One page glossary as required 

## 7. Contributions

An one page statement of contributions, including a list of each member of the group and what they contributed to this document.

---

## Formatting Rules 

 * Write your document using [Markdown](https://gitlab.ecs.vuw.ac.nz/help/user/markdown#gitlab-flavored-markdown-gfm) in your team's GitLab repository.
 * Major sections should be separated by a horizontal rule.

## Assessment 

This document will be weighted at 20% on the architectural proof-of-concept(s), and 80% on the architecture design.

The proof-of-concept will be assessed for coverage (does it demonstrate all the technologies needed to build your project?) and quality (with an emphasis on simplicity, modularity, and modifiability).

The document will be assessed by considering both presentation and content. Group and individual group members will be assessed by identical criteria, the group mark for the finished PDF and the individual mark on the contributions visible through `git blame`, `git diff`, file histories, etc. 

The presentation will be based on how easy it is to read, correct spelling, grammar, punctuation, clear diagrams, and so on.

The content will be assessed according to its clarity, consistency, relevance, critical engagement and a demonstrated understanding of the material in the course. We look for evidence these traits are represented and assess the level of performance against these traits. Inspection of the GitLab Group is the essential form of assessing this document. While being comprehensive and easy to understand, this document must be reasonably concise too. You will be affected negatively by writing a report with too many pages (far more than what has been suggested for each section above).

---

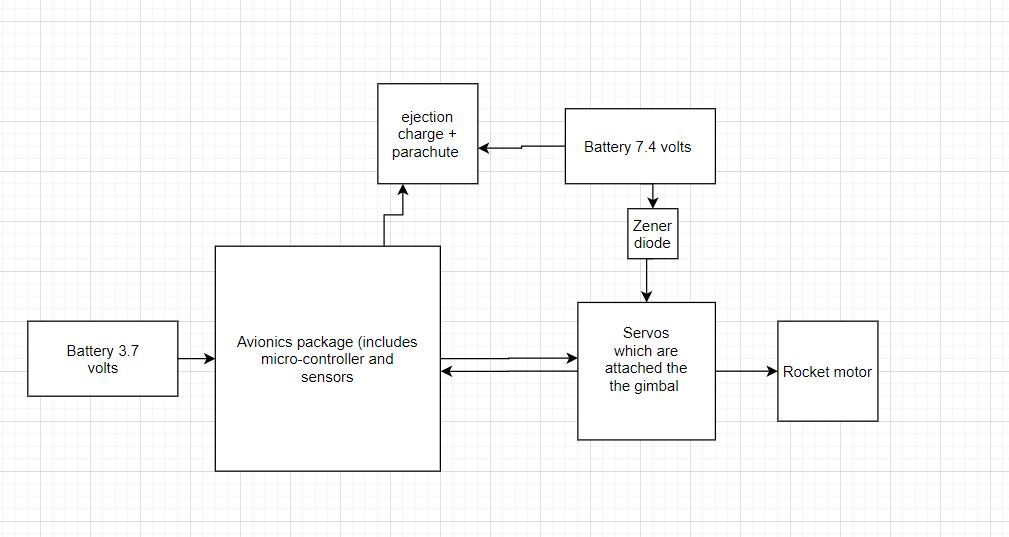
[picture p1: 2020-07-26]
Hardware_Development/Hardware Block Diagrams/Rocket_Block_Diagram.jpg

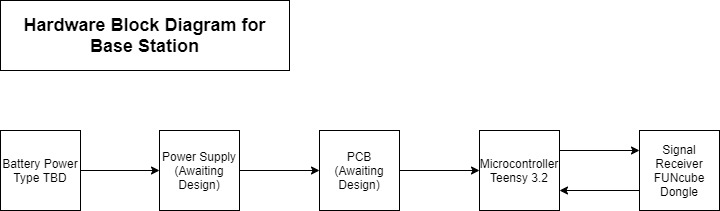
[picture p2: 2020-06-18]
Hardware_Development/Hardware Block Diagrams/Base_Station_Diagram.jpg

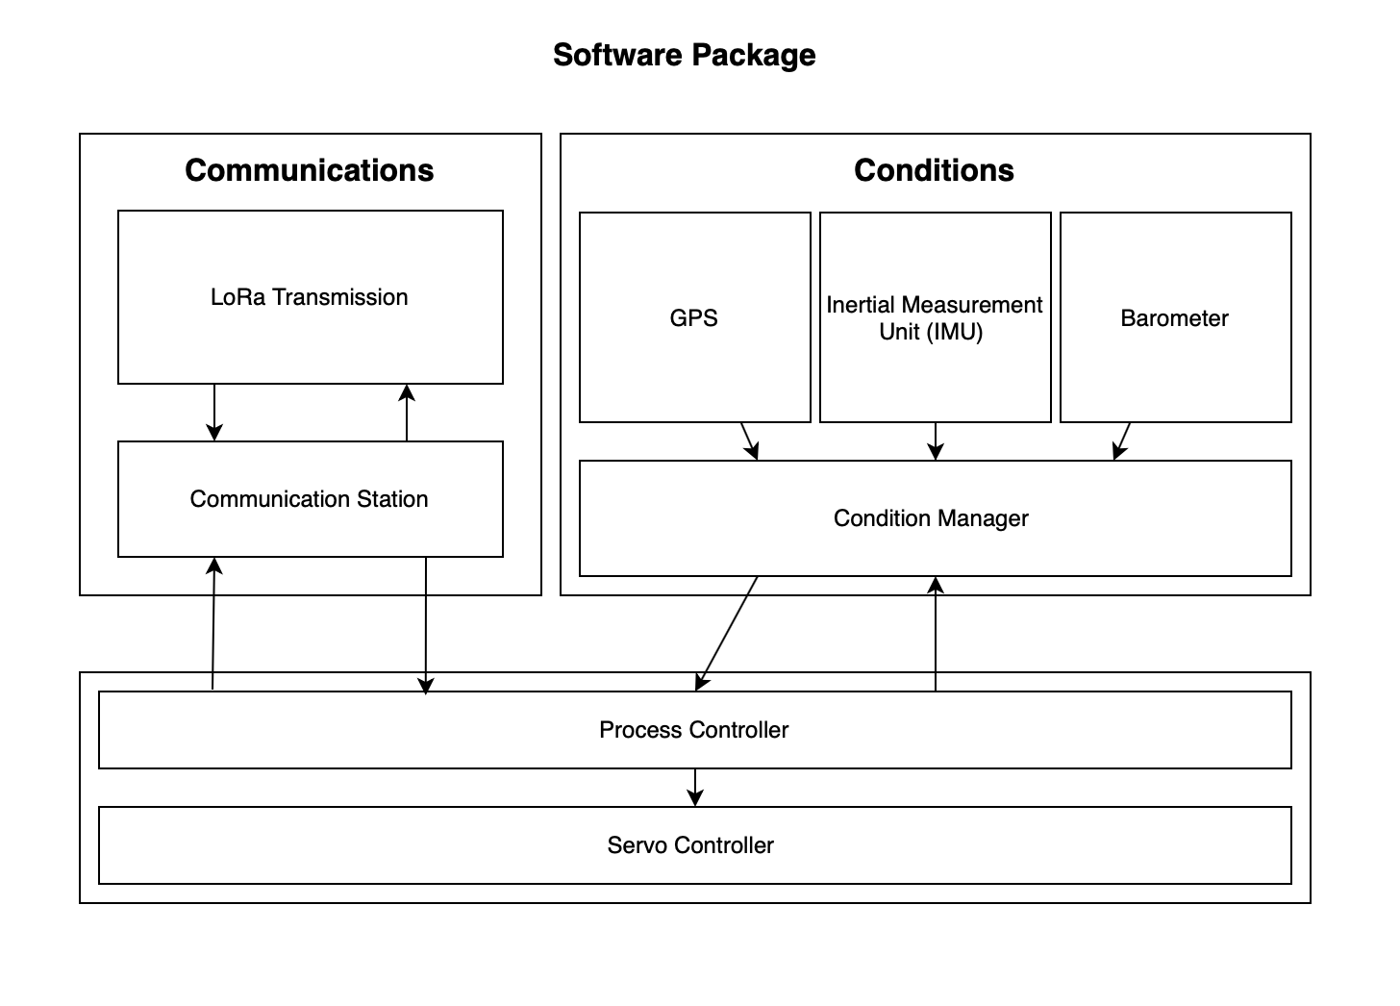
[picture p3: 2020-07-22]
Extra files/FeatureArchitecture.png

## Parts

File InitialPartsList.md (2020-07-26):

|Supplier|	Supplier Part Number|	Manufacturer Part Number|	Qty|	Description|	Price Indivdual|	Total (NZD)|
|---|---|---|-----|-----|-----|---|
|Digi-key|		1738-1232-ND|		SER0011|	2|	"		DC Motor Servomotor, RC (Hobby) 6VDC"|	14.4095|	28.819|
|Digi-key|	1597-1491-ND|	109990165|	2|	"General ISM < 1GHz LoRa™ Transceiver Module 433MHz Surface Mount	|	14.6625|	29.325|
|Digi-key|	1528-3886-ND|	3886|	1 |	MPU-6050 - Accelerometer, Magnetometer Sensor Evaluation Board|	14.375|	14.375|
|Digi-key|	1528-4382-ND|	4382|	1 |	STM32F405 Feather STM32F405 Express STM32F4 ARM® Cortex®-M4 MCU 32-Bit Embedded Evaluation Board|	51.6005|	51.6005|
|Digi-key|	1528-1034-ND|	1893|	1 |	MPL3115A2 - Pressure, Temperature Sensor Evaluation Board|	$20.57|	20.5735|
|Digi-key|	123-A-USB31C-20A-050A-ND |	A-USB31C-20A-050A|	1 |	USB 3.1 Type C to A Cable|	$6.05|	6.05|
|Mr Positive|	N/A |	SKU: F182|	1 |	7.4v 500mah DiFeida Quadrocopter Lipo Battery|	$23.00|	23.00|

| Component | Purpose |  Price(NZD) |
|---|---|---|
| TBC | Microcontroller for base station | dependin  |
| 3D printing | Parts for rocket | depending |
| PCB | Cicuitry for rocket and/or base station | depending |
| 2S 7.4V Battery  | To power rocket | ~$10 | 
| Radio transceiver| RFM90 | ~$28 |
| GPS | MPA\uc0\u8209 154\u8209 ANT L1 GPS | $9.4 |
| LMZM23600V3SIL | Main Component/ICU in power supply | $2.60 |
| GRM31CR61C106KA88L | Stabilizing Component for power supply | ~$0.12 | 
| C3216X5R1E476M160AC | Stabilizing Component for power suppl | ~$0.61 |

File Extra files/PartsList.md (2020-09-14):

|Supplier|	Supplier Part Number|	Manufacturer Part Number|	Qty|	Description|	Price Indivdual|	Total (NZD) incl GST|
|---|---|---|-----|-----|-----|---|
|Digi-key|		1738-1232-ND|		SER0011|	2|	"		DC Motor Servomotor, RC (Hobby) 6VDC"|	14.4095|	28.819|
|Digi-key|	1597-1491-ND|	109990165|	2|	"General ISM < 1GHz LoRa™ Transceiver Module 433MHz Surface Mount	|	14.6625|	29.325|
|Digi-key|	1528-3886-ND|	3886|	1 |	MPU-6050 - Accelerometer, Magnetometer Sensor Evaluation Board|	14.375|	14.375|
|Digi-key|	1528-4382-ND|	4382|	1 |	STM32F405 Feather STM32F405 Express STM32F4 ARM® Cortex®-M4 MCU 32-Bit Embedded Evaluation Board|	51.6005|	51.6005|
|Digi-key|	1528-1034-ND|	1893|	1 |	MPL3115A2 - Pressure, Temperature Sensor Evaluation Board|	$20.57|	20.5735|
|Digi-key|	123-A-USB31C-20A-050A-ND |	A-USB31C-20A-050A|	1 |	USB 3.1 Type C to A Cable|	$6.05|	6.05|
|Mr Positive|	N/A |	SKU: F182|	1 |	7.4v 500mah DiFeida Quadrocopter Lipo Battery|	$23.00|	23.00|
|Mr Positive|	N/A |	SKU: GP37580GT|	1 |	Giant Power 1s 3.7v 580mah 25c 1-24 Carisma |	$13.00|	13.00|
|Seed Studio|	N/A |	SKU: 113020003|	1 |	Grove - GPS Module |	$40.595|	40.595|

| Component | Purpose |  Price(NZD) |
|---|---|---|
| TBC | Microcontroller for base station | dependin  |
| 3D printing | Parts for rocket | depending |
| PCB | Cicuitry for rocket and/or base station | depending |
| 2S 7.4V Battery  | To power rocket | ~$10 | 
| Radio transceiver| RFM90 | ~$28 |
| GPS | MPA\uc0\u8209 154\u8209 ANT L1 GPS | $9.4 |
| LMZM23600V3SIL | Main Component/ICU in power supply | $2.60 |
| GRM31CR61C106KA88L | Stabilizing Component for power supply | ~$0.12 | 
| C3216X5R1E476M160AC | Stabilizing Component for power suppl | ~$0.61 |

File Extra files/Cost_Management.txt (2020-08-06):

Cost Management Document:

This doc contains all current funds spent on parts and remains funds for the
project. Further information on specific parts and orders can be found in the
past list document.

Initial Funds $300.

Costs:
	- 2x DC servo motor ($14.4095 ea)	$28.819
	- 2x Tx Rx Module ($14.6625 ea) 	$29.235
	- MPU-6050 				        	$14.375
	- STM32F405 Feather		        	$51.605
	- MPL3115A2					        $20.57
	- USB C Cable			        	$6.05
	- 7.4v Battery				        $23
	- 3.7v Battery				        $10

Total Spent:					    	$193.654

Total Remaining:					    $106.34

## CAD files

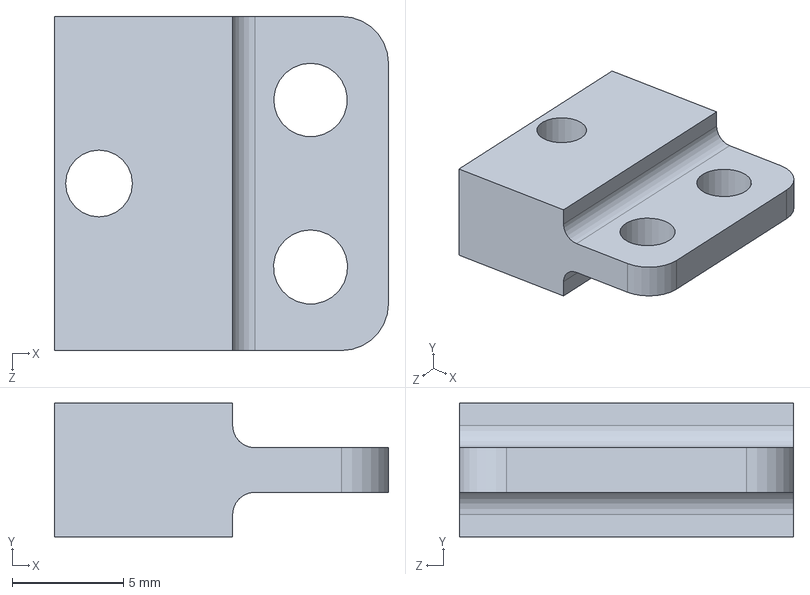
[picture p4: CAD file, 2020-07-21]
Hardware_Development/Gimbal_Design/ServpAdapterB.SLDPRT
15.0 x 6.00 x 15.0 mm

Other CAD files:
Hardware_Development/Gimbal_Design/ServoAdapter.SLDPRT
Hardware_Development/Gimbal_Design/MotorCaseComponent.sldprt
Hardware_Development/Gimbal_Design/PitchComponent.sldprt
Hardware_Development/Gimbal_Design/YawComponent.sldprt

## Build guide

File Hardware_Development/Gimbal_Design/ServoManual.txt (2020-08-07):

Setting up and Test Servo Motors - GS-9025MG

-Red is V++ (6V), Brown is Ground, Orange is PWM input
-Functioning at 50HZ PWM
-Duty Cycle vary from 0.45ms - 2.5ms, 2.25% - 12.5
-Tested response when PWM is changed without source power then source power 
switched on. Servo responded instanteously, which is ideal if the power is to
ever change.
-Middle point for the Yaw Servo was set 1.4ms
-Same for the Pitch Servo, @ 1.4ms
-Pitch Axis Gimbal Operating Cycle: 1.19ms-159ms.
-Yaw Axis Gimbal Operating Cycle: 1.05ms-159ms.
-These are duty cycles that have the gimbal operating at maximum angles, these
should not be exceeded as it will potentially damage the gimbal.

Resistance, determined from the datasheet (6V):
-24 ohms @  at stopped
-6 ohms @ no load

From this anaylsis we can determine how we are going to control the servos from
the MCU. By producing a modulated 50Hz square wave, aka PWM, on one of the pins
we will be able to replocate these lab results. From the software integration we
should ideally be able to set the duty cycle of the PWM and therefore set the
angle of the servos individually.

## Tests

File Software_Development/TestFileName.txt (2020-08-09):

This is just an empty file to update the folder name in Git

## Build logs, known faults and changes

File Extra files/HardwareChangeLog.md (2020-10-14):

# Hardware Change Log

16/7/20: First batch of components arrived and stored in lab.

22/7/20: Assembled first prototpye of gimbal.

24/7/20: Soldered headers onto the microcontroller breakout for prototyping.

29/7/20: Soldered headers onto the two of the sensor boards (IMU + barometer). 

29/7/20: Feater controller and servo motors tested on breadboard. Proper operation has been confirmed.

05/08/20: Sean and Jason designed voltage regulator from batteries to servo motors.

5/8//20: Feather configured with PlatformIO on the computers of two of the group members.

6/8/20: Test sketch confirming the MCU can control the gimbal servos via PWM and external PSU.

20/8/20: Got HAL framework setup as a possible option.

24/8/20: Got USB-Serial debug statements working between IDE and the Feather. 

11/9/20: Test program for IMU is working.

11/9/20: Configure wiring onto breadboard.

11/9/20: Soldered wires for LoRa TX

18/9/20: Successful build of temperature/barometer sensor board.

04/10/20: Calibrated gyro algorithm.

09/10/20: Gyroscope orientation has direct control over servos.

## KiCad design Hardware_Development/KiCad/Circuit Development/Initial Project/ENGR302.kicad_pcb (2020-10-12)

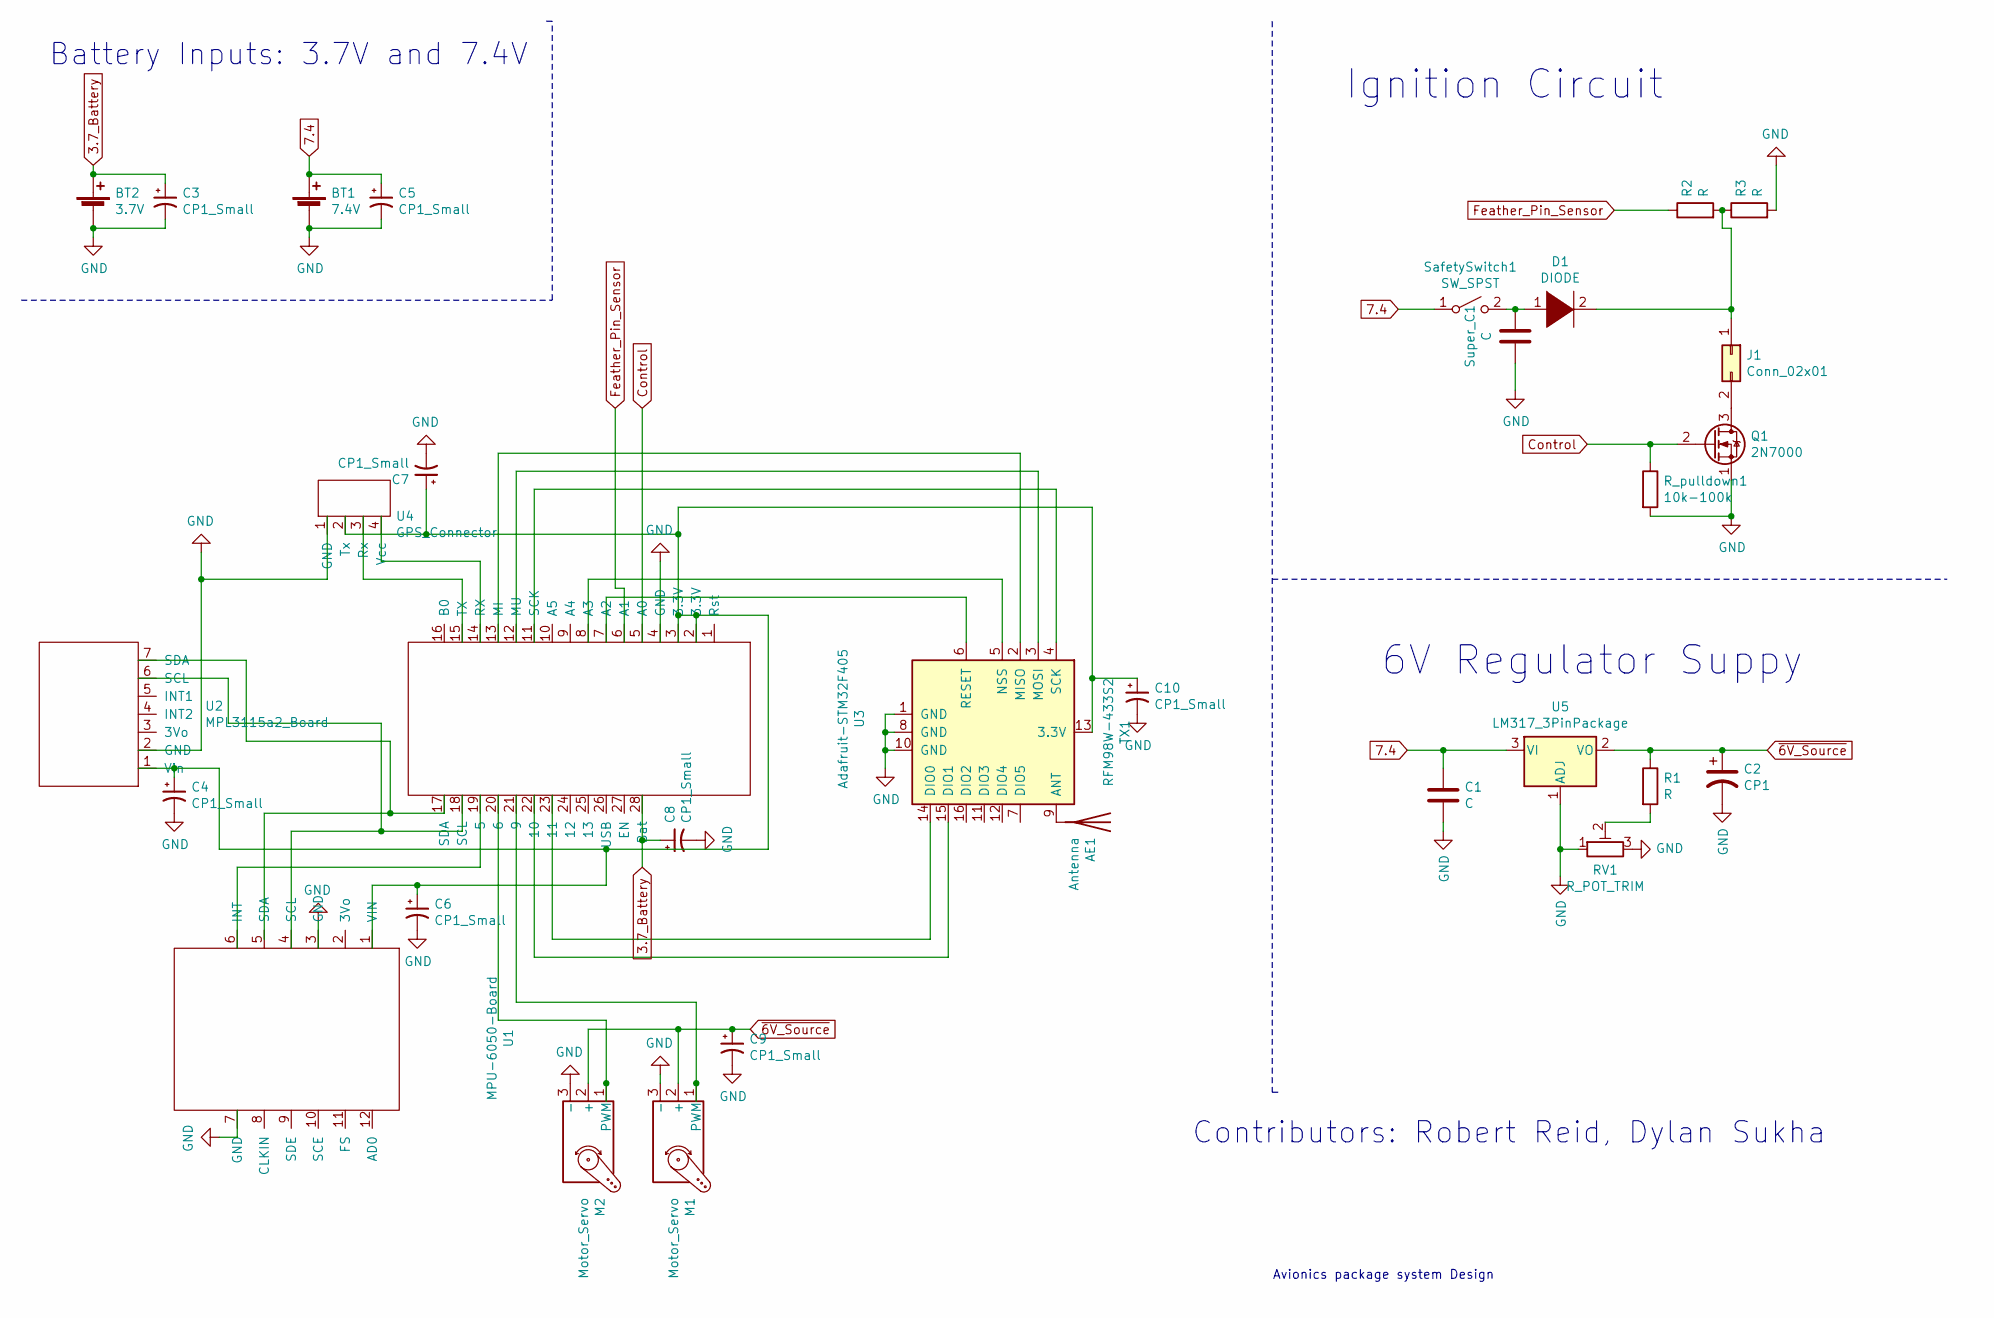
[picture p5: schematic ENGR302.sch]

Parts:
AE1: Antenna; PinHeader_1x01_P2.54mm_Vertical
BT1: 7.4V; PinHeader_1x02_P2.54mm_Vertical
BT2: 3.7V; PinHeader_1x02_P2.54mm_Vertical
C1: C; C_Axial_L3.8mm_D2.6mm_P10.00mm_Horizontal
C2: CP1; C_Axial_L3.8mm_D2.6mm_P10.00mm_Horizontal
C3, C5, C6, C7, C8, C10: CP1_Small; CP_Radial_D4.0mm_P2.00mm
C4, C9: CP1_Small; C_Axial_L3.8mm_D2.6mm_P7.50mm_Horizontal
D1: DIODE; Diode_DO-35_P10mm
J1: Conn_02x01; PinHeader_1x02_P2.54mm_Vertical
M1, M2: Motor_Servo; PinHeader_1x03_P2.54mm_Vertical
Q1: 2N7000; PinHeader_1x03_P2.54mm_Vertical
R1, R2, R3: R; R_Axial_DIN0204_L3.6mm_D1.6mm_P7.62mm_Horizontal
RV1: R_POT_TRIM; PinHeader_1x03_P2.54mm_Vertical
R_pulldown1: 10k-100k; R_Axial_DIN0204_L3.6mm_D1.6mm_P7.62mm_Horizontal
SafetySwitch1: SW_SPST; PinHeader_1x02_P2.54mm_Vertical
Super_C1: C; C_Axial_L5.1mm_D3.1mm_P10.00mm_Horizontal
TX1: RFM98W-433S2; XCVR_RFM98W-433S2
U1: MPU-6050-Board; MPU_6050_Board
U2: MPL3115a2_Board; mpl3115a2
U3: Adafruit-STM32F405; Adafruit_Feather
U4: GPS_Connector; PinHeader_1x04_P2.54mm_Vertical
U5: LM317_3PinPackage; PinHeader_1x03_P2.54mm_Vertical

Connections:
3.7_Battery: BT2.1 (+), C3.1, C8.1, U3.28 (Bat)
7.4: BT1.1 (+), C1.1, C5.1, SafetySwitch1.1 (A), U5.3 (VI)
Control: Q1.2 (G), R_pulldown1.1, U3.5 (A0)
Feather_Pin_Sensor: R2.1, U3.6 (A1)
GND: BT1.2 (-), BT2.2 (-), C1.2, C2.2, C3.2, C4.2, C5.2, C6.2, C7.2, C8.2, C9.2, C10.2, M1.3 (-), M2.3 (-), Q1.1 (S), R3.2, RV1.1, RV1.3, R_pulldown1.2, Super_C1.2, TX1.1 (GND), TX1.8 (GND), TX1.10 (GND), U1.3 (GND), U1.7 (GND), U2.2 (GND), U3.4 (GND), U4.1 (GND), U5.1 (ADJ)
unnamed: AE1.1, TX1.9 (ANT)
unnamed: C4.1, C6.1, C7.1, C10.1, TX1.13 (3.3V), U1.1 (VIN), U2.1 (Vin), U3.2 (3.3V), U3.3 (3.3V), U4.2 (Tx)
unnamed: D1.1 (K), SafetySwitch1.2 (B), Super_C1.1
unnamed: D1.2 (A), J1.1, R2.2, R3.1
unnamed: J1.2, Q1.3 (D)
unnamed: M1.1 (PWM), U3.21 (9)
unnamed: M2.1 (PWM), U3.20 (6)
unnamed: R1.2, RV1.2
unnamed: TX1.2 (MISO), U3.13 (MI)
unnamed: TX1.3 (MOSI), U3.12 (MU)
unnamed: TX1.4 (SCK), U3.11 (SCK)
unnamed: TX1.5 (NSS), U3.8 (A3)
unnamed: TX1.6 (RESET), U3.7 (A2)
unnamed: TX1.14 (DIO0), U3.23 (11)
unnamed: TX1.15 (DIO1), U3.22 (10)
unnamed: U1.4 (SCL), U2.6 (SCL), U3.18 (SCL)
unnamed: U1.6 (INT), U3.19 (5)
unnamed: U2.7 (SDA), U3.17 (SDA)
unnamed: U3.14 (RX), U4.4 (Vcc)
unnamed: U3.15 (TX), U4.3 (Rx)
~6V_Source: C2.1, C9.1, M1.2 (+), M2.2 (+), R1.1, U5.2 (VO)

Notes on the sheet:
Avionics package system Design
Contributors: Robert Reid, Dylan Sukha
Battery Inputs: 3.7V and 7.4V
Ignition Circuit
6V Regulator Suppy

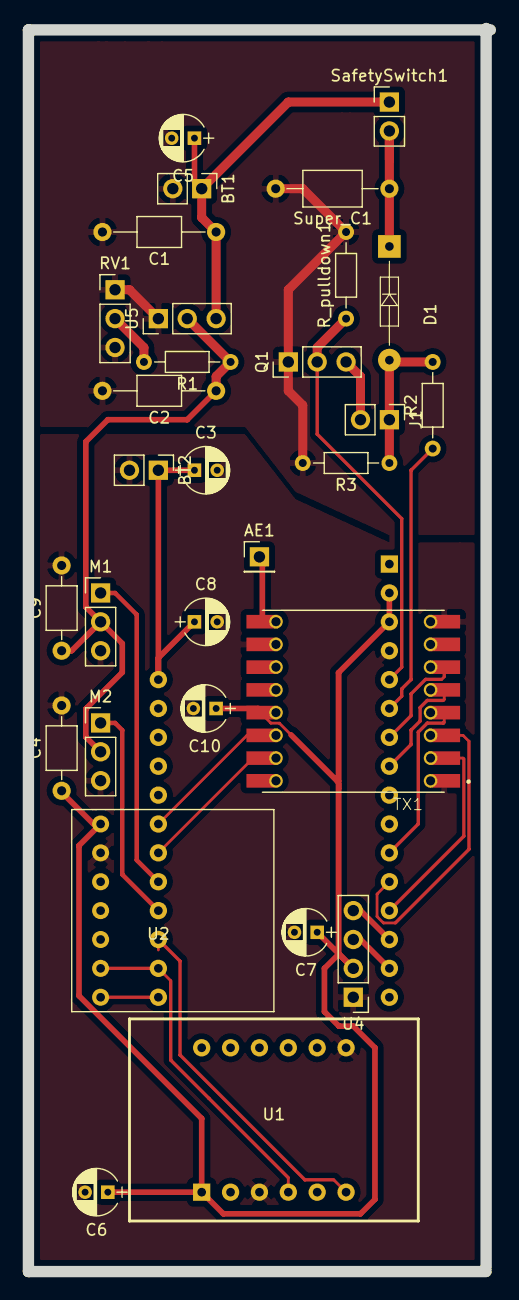
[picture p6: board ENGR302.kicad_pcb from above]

Board: 2 copper layers, 40.6 x 109.3 mm, 31 parts (1 on the bottom side), 26 nets.

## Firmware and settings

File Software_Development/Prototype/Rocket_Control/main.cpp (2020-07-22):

#include "RocketControl.h"
#include <stdio.h>
#include <string>

float target = 4.5569;
float changeBound = 10;

/**
 * Checks if two float values are equal. Takes into account -0 and assigns it as 0.
 *
 * @param val1  float   The first value to compare
 * @param val2  float   The second value to compare
 * @return True if both values are equal (including -0 and 0 being equal)
 */
bool equals(float val1, float val2){
    val1 = (val1 == -0 ? 0 : val1);
    val2 = (val2 == -0 ? 0 : val2);

    return val1 == val2;
}

int main() {
    RocketControl c(target, changeBound, 1, 1, 0);

    float dir = 125;
    float wdir = dir;
    for(int i=0; i<1000; i++){
        printf("Iteration: %d\n", i);
        wdir++;
        dir += c.getBoundedAdjustment(dir);
        printf("With PID: %.2f\t\tWithout PID: %.2f\n\n", dir, wdir);
    }

    std::string s = (dir == target) ? "Target Reached" : "Failed to Reach Target";
    printf("%s\nFinal Value: %.2f\t\tIntended Target: %.2f\n", s.c_str(), dir, target);

    return 0;
}

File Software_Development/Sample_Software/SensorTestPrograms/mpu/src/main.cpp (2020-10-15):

#include <Arduino.h>

/** IMU-Controlled Servo Orientation.
 * Rocket is placed upright vertically. 
 * Orientation is calibrated at 0 degrees for two axis.
 * 
 * Required duty cycle is then calculated to drive the servos.
 * 
 * Other 'main copy.txt' was the original test program that
 * just recorded angular velocity, not position.
 */

#include <Adafruit_MPU6050.h>
#include <Adafruit_Sensor.h>
#include <Wire.h>

Adafruit_MPU6050 mpu;

const int MPU_addr = 0x68;
int16_t AcX, AcY, AcZ, Tmp, GyX, GyY, GyZ; //int16_t

int minVal = 265;
int maxVal = 402;

double x;
double y;
double z;
double baseX;
double baseY;
double baseZ;

float Tp = 50; //Duty cycle period (20 Hz), is later converted to 60 Hz.
float tdc = 25; //uint_8

void setup()
{
  Wire.begin();
  Wire.beginTransmission(MPU_addr);
  Wire.write(0x6B);
  Wire.write(0);
  Wire.endTransmission(true);
  Serial.begin(9600);

  Wire.beginTransmission(MPU_addr);
  Wire.write(0x3B);
  Wire.endTransmission(false);
  Wire.requestFrom(MPU_addr, 14, true);
  AcX = Wire.read() << 8 | Wire.read();
  AcY = Wire.read() << 8 | Wire.read();
  AcZ = Wire.read() << 8 | Wire.read();
  int xAng = map(AcX, minVal, maxVal, -90, 90);
  int yAng = map(AcY, minVal, maxVal, -90, 90);
  int zAng = map(AcZ, minVal, maxVal, -90, 90);
  baseX = RAD_TO_DEG * (atan2(-yAng, -zAng) + PI);
  baseY = RAD_TO_DEG * (atan2(-xAng, -zAng) + PI);
  baseZ = RAD_TO_DEG * (atan2(-yAng, -xAng) + PI);
  pinMode(5, OUTPUT);
}
float angyX(double baseAng, double ang) {
  double zing = (baseAng - ang);
  if (zing>180) zing = zing-360;
  return zing;
}

float angyY(double baseAng, double ang) {
  double zing = (double)abs((baseAng - ang));
  if (zing>180) zing = zing-360;
  //Serial.printf("B:A %i %i", baseAng, ang);
  return zing;
}

void loop()
{
  Wire.beginTransmission(MPU_addr);
  Wire.write(0x3B);
  Wire.endTransmission(false);
  Wire.requestFrom(MPU_addr, 14, true);
  AcX = Wire.read() << 8 | Wire.read();
  AcY = Wire.read() << 8 | Wire.read();
  AcZ = Wire.read() << 8 | Wire.read();
  double xAng = map(AcX, minVal, maxVal, -90, 90);
  double yAng = map(AcY, minVal, maxVal, -90, 90);
  double zAng = map(AcZ, minVal, maxVal, -90, 90);

  //delay(700);

  x = RAD_TO_DEG * (atan2(-yAng, -zAng) + PI);
  y = RAD_TO_DEG * (atan2(-xAng, -zAng) + PI);
  z = RAD_TO_DEG * (atan2(-yAng, -xAng) + PI);



  /*Serial.print("AngleX= ");
  Serial.println(angyX(baseX,x));

  Serial.print("AngleY= ");
  Serial.println(angyY(baseY,y));

  Serial.println("-----------------------------------------"); 
  delay(300);*/
  
  
  /*
    Duty-cycle of 6% positions the servo at midpoint, 90 degrees. 
    0% is 0 degrees, 12% is 180 degrees. 

    The current code is a proof of functionality expirement. 
    It is currently implemented with a polling approach. 
    For greater responsivness upon integration with the wider avionics system,
     It is strongly advised to call this module via timer-based interrupts. 
  */
  double xxAng = (angyX(baseX,x));
  if(xxAng>0) {
    if (xxAng > 10) xxAng = 10;
    tdc = 3 + (Tp*xxAng/180) * 0.12; //Where the '3' constant is 6%. (3/50).
    //Serial.println(tdc);
  }
  else if(xxAng<0) {
    if (xxAng < -10) xxAng = -10;
    tdc = 3 + (Tp*xxAng/180) * 0.12;
    //Serial.println(tdc);
  }

  digitalWrite(5, HIGH);
  delay(tdc/3);
  digitalWrite(5, LOW);
  delay((Tp-tdc)/3);
}

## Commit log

2020-04-18 Update project-requirement.md
    I wrote some content for Introduction 1.1 and 1.2 however I am unsure what the correct terminology is for the combustion part of the rocket that thrusts it in the atmosphere, keeps it going and controls where it goes. I doubt "exhaust" is the correct term.
2020-04-24 Update project-requirement.md
    Added capital letter for the word "Teensy"
2020-05-14 3.6 one para missing
2020-05-16 Finished main stages of functions.
2020-05-19 Test Markup
    I am going to try making the nested list points ordered instead of unordered. The problem I am trying to solve is the nested list keeps appearing closer to the next primary element (the attribute title) instead of its current one.
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2020-06-16 Resolved all the threads.
2020-06-18 Directory for prototype related resources
2020-06-18 Added Software Prototype Project
    Created blank template for the project
2020-06-18 Removed PID Demo
    Going to retry with regular C++
2020-06-18 Started Rocket PID Prototype
    I'm trying this again
2020-06-18 Added Minor Updates to the PID Controller
    Currently, I'm working out the kinks to the PID controller
2020-06-18 Added More Content to the PID
    Added more content to the PID prototype. I am now trying to fine tune it.
2020-06-18 Added Change Bounds
    Added adjustment bounds using the PID controller. This is to simulate the restrictions of a real life controller.
2020-06-19 Added Fail Safe for Buffer Overflows when adding to the Integral Value
    Following Jolon's recommendations, I added that fail-safe recommendation to ensure if a buffer overflow occurs, the maximum possible value is used to store the integral value.
    [main.cpp]
2020-07-20 Servo adapter, using smaller servo which does not fit with the original Gimbal Design, so adapter to account for size difference
    [ServoAdapter.SLDPRT]
2020-07-20 Yam component of Gimbal
    [YawComponent.sldprt]
2020-07-20 Pitch Component of Gimbal
    [PitchComponent.sldprt]
2020-07-20 Motor Case Component of Gimbal
    [MotorCaseComponent.sldprt]
2020-07-21 Replace ServoAdapter.SLDPRT with new version, included rounded edges and fixed small imperfections
    [ServoAdapter.SLDPRT]
2020-07-21 Other part of the servo adapter, final design
    [ServpAdapterB.SLDPRT]
2020-07-21 Start ReadMe file for 3D printable Gimbal Parts
2020-07-22 Hello World Code
    Created code that successfully compiled and got uploaded to the board
2020-07-26 Added More Configuration Content
    I've configured the build stage to do somethings. Currently it doesn't compile code yet.
2020-07-26 Added code to List current directory
2020-07-26 Switched Dockerfile to Ubuntu
2020-07-26 Returned the Dockerfile back to Apline
    Tried using Linux, didn't go so well and it seems heavy. Switching back to Apline. This time I am adjusting the file to install dependencies using the Alpine APK instead of Debian's apt-get
2020-07-26 Switching back to Ubuntu
    Turns out many of the resources needed by PlatformIO is better run on Ubuntu
2020-07-26 Switching to Pip3 to be installed
2020-07-26 Minor adjustments
    Added the -y flag for apt-get and switched one use of pip to pip3
2020-07-26 Switching the Build Process to the Docker Runner
2020-07-26 Removed the Deploy Stage as we have nothing to Deploy to
2020-07-26 Started Pipeline for KiCad Verification
    [MotorCaseComponent.sldprt, PitchComponent.sldprt, ServoAdapter.SLDPRT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]
2020-07-26 Removed checks for KiCad
    I am going to consult with the class if anyone knows of a way to verify KiCad projects via the command line.
2020-07-27 Rutile Servo Manager
    Added empty library for the servo manager
2020-07-27 Created basic skeleton code for rhodonite (external sensors)
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2020-07-27 Servo manual to determine duty cycles and voltages for operations
2020-07-28 Added constructor and a few variables into the rhodonite code as a start The variables so far only cover part of the sensors, particularly the GPS ans barometer. These are subject to be being changed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
2020-08-03 Adding a variable for IMU to the rhodonite code
2020-08-06 Upload New File
    [ENGR302.sch]
2020-08-06 Added photos showing results of work in lab connecting the development board to servos
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2020-08-09 Moved the Sample LoRa Code into the Software folder
2020-08-09 Added Sample File to update folder name
    Long story short, I've updated the folder name from "software" to "Software" however I'm trying to get GitLab to synchronise those changes.
2020-08-10 Removed Duplicate Library
    Somehow we ended up with 2 Rutile (Servo) libraries. I removed the empty duplicate.
2020-08-14 WIP: Lots of Improvements in Progress
    Committing this to the repo before I forget. I am currently working on this.
    Here is what I have done so far:
    * Moved function definitions from header files in Rutile and Rhodonite packages to their respective class files.
    * Added Serial Printer functions
    * Reorganised how libraries are defined in header files. 'lars_main.h' got split into two files: 'lars_main.h' and 'fluoride_dependencies.h'. They were then placed into their own directories. The former fetches all the packages, the latter fetches commonly used libraries across packages.
    * Attempting to implement a error handler
    [main.cpp]
2020-08-14 Rutile (Servo Controller) Code Correction & Error Handling
    Implemented an error handler for the Servo Controller so that if an invalid value was given (values not between 0 and 359), it sends an error message via the error handler to the Serial port.
    I also tidied the code a little for improve stability.
2020-08-14 WIP: Changed the Error Handler to Diagnostic Handler
    Work in progress and will not build yet. I have changed the Error Handler to a Diagnostic Handler and added a feature where a message can be reported as well as an error.
    Currently stuck on the Padparadscha object not being passed through the constructor.
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2020-09-02 Attempting to Include Library for LoRa
    Attempting to make the sample code @reidrobe provided work.
2020-09-02 Removed Includes and Implementation attempts of RH_RF95.h
    This library seems to not be compatible with the STM32 in its current form. In the meantime, I will remove it from the main project until we can get a working prototype compiling in a separate projec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
    Removing this will allow the pipeline to complete.
2020-09-03 Including Actuators in Design
    [ENGR302.sch]
2020-09-04 Started connections
    [ENGR302.sch]
2020-09-06 Testing LoraLib library for LoRa Attempting to include the LoRaLib library so that the sample code provided compiles and runs properly
2020-09-07 Organising components and adding connections
    [ENGR302.sch]
2020-09-07 Included Zener diode Power regulator
    [ENGR302.sch]
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2020-09-09 Tested the Hello World Project
    Currently it works on an Arduino Uno but not for the STM32. I am not sure what is happening
2020-09-14 New iteration of wiring and including LoRa TX into design
    [ENGR302.sch]
2020-09-14 adding basestation RX and incl labels
    [ENGR302.sch]
2020-09-23 Design and Include Ignition Circuit for Parachute
    [ENGR302.sch]
2020-09-23 Included pulldown R on mosfet and Sensing line for Ignition
    [ENGR302.sch]
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2020-10-01 Updated MPU calibration sample, still need to calculate the duty cycle output.
2020-10-06 Finalising pin layout and assigning pins
    [ENGR302.sch]
2020-10-06 Adding final pin layout and assigning footprints
    [ENGR302.sch]
2020-10-07 PCB Design
    [ENGR302.sch]
2020-10-07 Include PCB File
    [ENGR302.kicad_pcb]
2020-10-08 Update single layer PCB, including decoupling caps
    [ENGR302.sch]
2020-10-12 Implementing size changes of board and track sizes
    [ENGR302.kicad_pcb, ENGR302.sch]
2020-10-12 Small changes to design of pcb
    [ENGR302.kicad_pcb]
2020-10-13 Uploaded the sample programs.
    MPL readings and IMU-Servo controls.
2020-10-19 Distribution of Docs Organised
    [ENGR302.kicad_pcb, ENGR302.sch, MotorCaseComponent.sldprt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]
2020-10-19 Renamed Software and Hardware Folders
    Replaced the space with an underscore.
    [ENGR302.kicad_pcb, ENGR302.sch, MotorCaseComponent.sldprt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]
2025-03-19 Updated README & Refactored Mentions of a Contributor to their current name
